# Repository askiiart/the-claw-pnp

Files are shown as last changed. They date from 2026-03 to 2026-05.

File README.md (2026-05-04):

# The Claw - pick-and-place head

A relatively cheap way to do manual pick and place by converting a 3D printer.

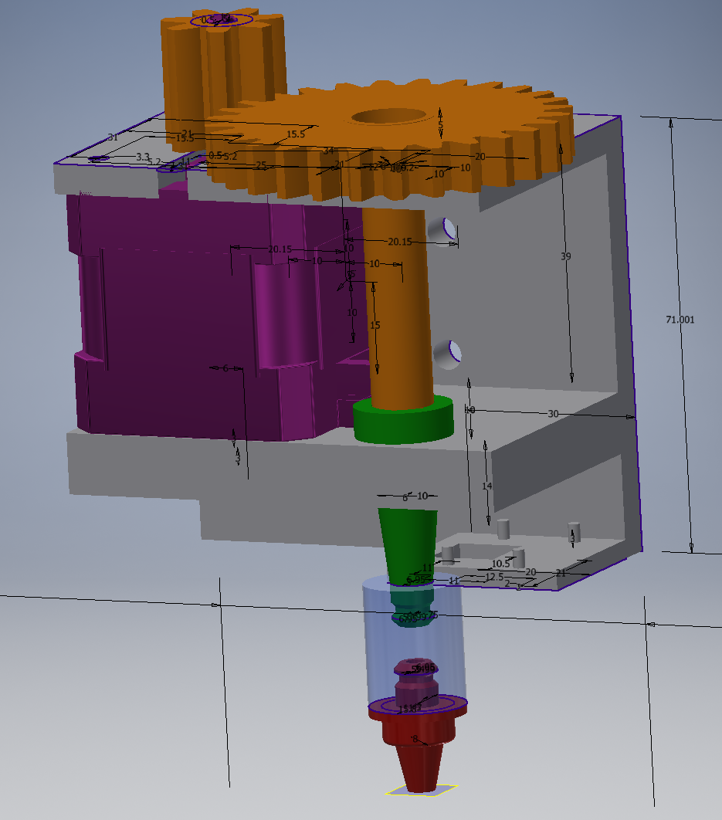
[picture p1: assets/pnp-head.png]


## Control/software

This just uses whatever Pi camera streaming software you want, plus Octoprint/serial to control it, like any printer. No special firmware is generally required (depending on your specific wiring). Octopi works great for this, as it provides both a camera view and serial/controls.

## Assembly

Just print all the parts, then assemble it all together. **Important**: Make sure you install the head on the printer before assembly, as the stepper motor blocks the screws.

Note: The solenoid controls vacuum on/off, that's not included on the head as it's extra weight as well as being hard to mount - put it near the air pump.

## Head assembly

- Screw in the stepper motor from the top
- Install the lower shaft (green) by just setting it in the bottom

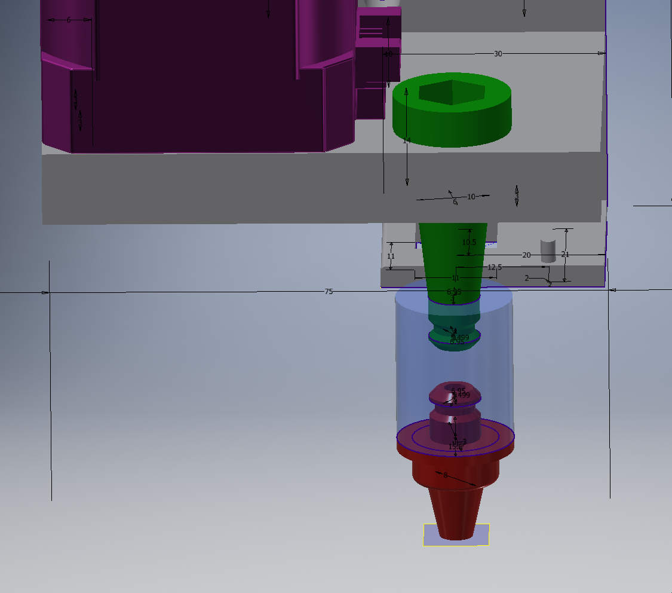
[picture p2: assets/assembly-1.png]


- There is a spring resting between the lower shaft and the roof (not shown in image). Install the upper shaft into the hole, connecting to the lower shaft, then install the small gear onto the stepper motor.

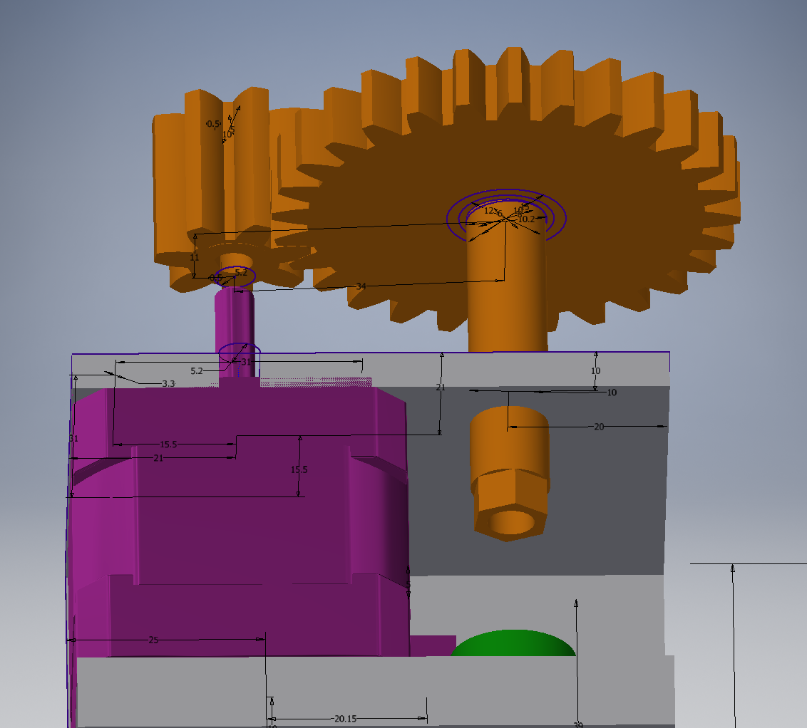
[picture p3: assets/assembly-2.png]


The nozzle is mounted using a silicone connector which has the lower shaft tip (juki nozzle connector) on one side, and the nozzle on the other to ensure proper fit. The silicone is used to make nozzles fit snugly - creating the mold is left as an exercise to the reader, as molding off a real nozzle will give the best results.

## Wiring

Your wiring can vary significantly, but the only control besides just basic movement is turning the solenoid on/off. If your fan headers can provide enough current, that will be the easiest way to control it.

## Parts

| Item name | Price | Quantity | Link | Total |
| --- | ----- | --- | --- | --- |
| NEMA 17 motor (XH) | 7.06  | 1 | <https://www.aliexpress.us/item/3256808273084374.html> | 7.06 |
| Spring (45x13) | 3.17  | 1 | <https://www.aliexpress.us/item/3256808172121056.html> | 3.17 |
| 6x8 5m tubing | 5.46  | 1 | <https://www.aliexpress.us/item/3256809523563550.html> | 5.46 |
| 24V Air pump | 11.4  | 1 | <https://www.aliexpress.us/item/3256807520990953.html> | 11.4 |
| Silicone | 25.62 | 1 | <https://www.amazon.com/BBDINO-Elastic-Silicone-Making-Casting/dp/B0DK9GD52Q> | 25.62 |
| AF-65 camera | 4.65  | 1 | <https://www.aliexpress.us/item/3256803200476731.html> | 4.65 |
| Solenoid | 5.88  | 1 | <https://www.aliexpress.us/item/3256807858795768.html> | 5.88 |
| 8x12x3.5mm bearing | 2.51  | 1 | <https://www.aliexpress.us/item/3256807442294068.html> | 2.51 |
| Blunt needles (nozzles) | 7.99  | 1 | <https://www.amazon.com/Dispensing-Industrial-Dispenser-Stainless-Adhesive/dp/B09CL4RB5X> | 7.99 |
| | | | | |
| | | | | |
| | | | | |
| Total | | | | 79.82355 |

---

Note: if trying to create an exploded view for assembly instructions, you want "Mate:9" - set it to e.g. 25mm.

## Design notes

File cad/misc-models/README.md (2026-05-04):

# Misc models

Models off grabcad and whatnot, just used for display in assembly and whatnot.

- [17HS4401](https://grabcad.com/library/17hs4401-1)

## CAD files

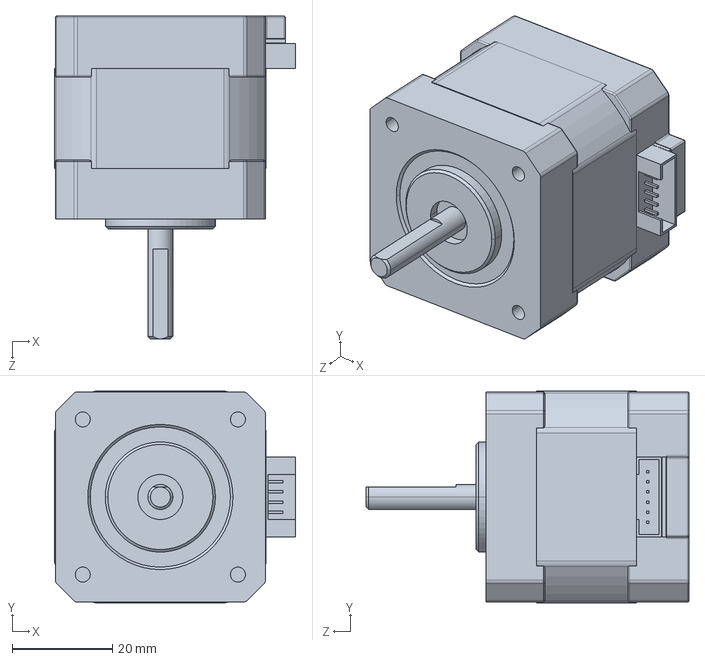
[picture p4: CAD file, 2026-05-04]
cad/misc-models/17HS4401.STEP
48.2 x 42.3 x 64.5 mm

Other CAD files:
cad/3mm-nozzle-assembly.iam
cad/5mm-nozzle-assembly.iam
cad/8mm-nozzle-assembly.iam
cad/gear-assembly.iam
cad/gear-assembly/Design Accelerator/Spur Gear11.ipt
cad/gear-assembly/Design Accelerator/Spur Gear21.ipt
cad/gear-assembly/Design Accelerator/Spur Gears1.iam
cad/juki-head-assembly.iam
cad/juki-mount.ipt
cad/juki-nozzle-base.ipt
cad/literally-just-a-cylinder-for-assembly-mockup-(silicone-sleeve).ipt
cad/literally-just-a-sketch.ipt
cad/misc-models/17HS4401.ipt
cad/motor-gear-base.ipt
cad/nozzle-3mm-tip.ipt
cad/nozzle-5mm-dip.ipt
cad/nozzle-8mm-dip.ipt
cad/pnp-head-assembly.iam
cad/pnp-head-assembly/Design Accelerator/Spur Gear12.ipt
cad/pnp-head-assembly/Design Accelerator/Spur Gear14.ipt
cad/pnp-head-assembly/Design Accelerator/Spur Gear22.ipt
cad/pnp-head-assembly/Design Accelerator/Spur Gear24.ipt
cad/pnp-head-assembly/Design Accelerator/Spur Gears2.iam
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

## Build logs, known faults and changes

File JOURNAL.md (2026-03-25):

# Journal

## 2026-03-22A - part selection and gantry plate

*1 hour*

Just had to grab the parts I had already researched prior - found motor dimensions [here](https://makers-hut.com/product/nema-8-hollow-shaft-stepper-motor-1-8deg-0-6a-18mnm-20x20x30mm-4-wire-nema8/).

motor dimensions

The image doesn't say everything, but given it's a standard NEMA 8 motor, it's easy to find dimensions

NEMA 8 dimensions

As for the gantry plate, found dimensions for that, from which I made a quick sketch of the relevant holes in Inventor.

gantry plate dimensions

holes in inventor

## 2026-03-22B - nozzle selection

*0.5 hours*

I found [this](https://groups.google.com/g/openpnp/c/s_PBSA7VQWM) usenet post, seems you can use all kinds of stuff as nozzles actually, including needles (for extruding glue and stuff). Since actual nozzles are expensive, I'll use those

## 2026-03-23A - camera selection and looked into motors more

*1 hour*

Spent some time trying to find which camera to use. Seems the best option is a pi camera-like module (65mm, autofocus, OV5647), so added that to the parts list. And given it's basically the same dimensions of a pi camera 2, I can design around that.

I also looked into motor selection more, turns out that motor I had previously selected is way too low voltage, I wouldn't be able to add a spring, and it's also more difficult to attach stuff to it given it's a smooth shaft. Instead, I'm going for a design similar to xpdiy's with a standard NEMA 17 motor, albeit with silicone to hold the nozzle for better fit, easier printing, and ease of design.

## 2026-03-23B - Designed the head, just need to design nozzle bits

*3 hours*

I designed the head, still need to design the nozzle bits but got a good start.

## 2026-03-24/25 - CAD yay

*7 hours*

So uh I actually got decent at CAD, even figured out how to do assembly somewhat competently. Not much to say here besides me just trying to figure out workarounds for Inventor being weird - I ended up creating a structure that would've made more sense as a loft by extruding and using the hole tool, and I even had to make a part that's literally just a sketch in order to align stuff in assembly.

Really not much to journal here unfortunately, besides just that I learned how to CAD half decently. Oh also fun fact apparently there isn't a single tutorial on how to use springs in Inventor, *everybody* just makes springs out of coils.

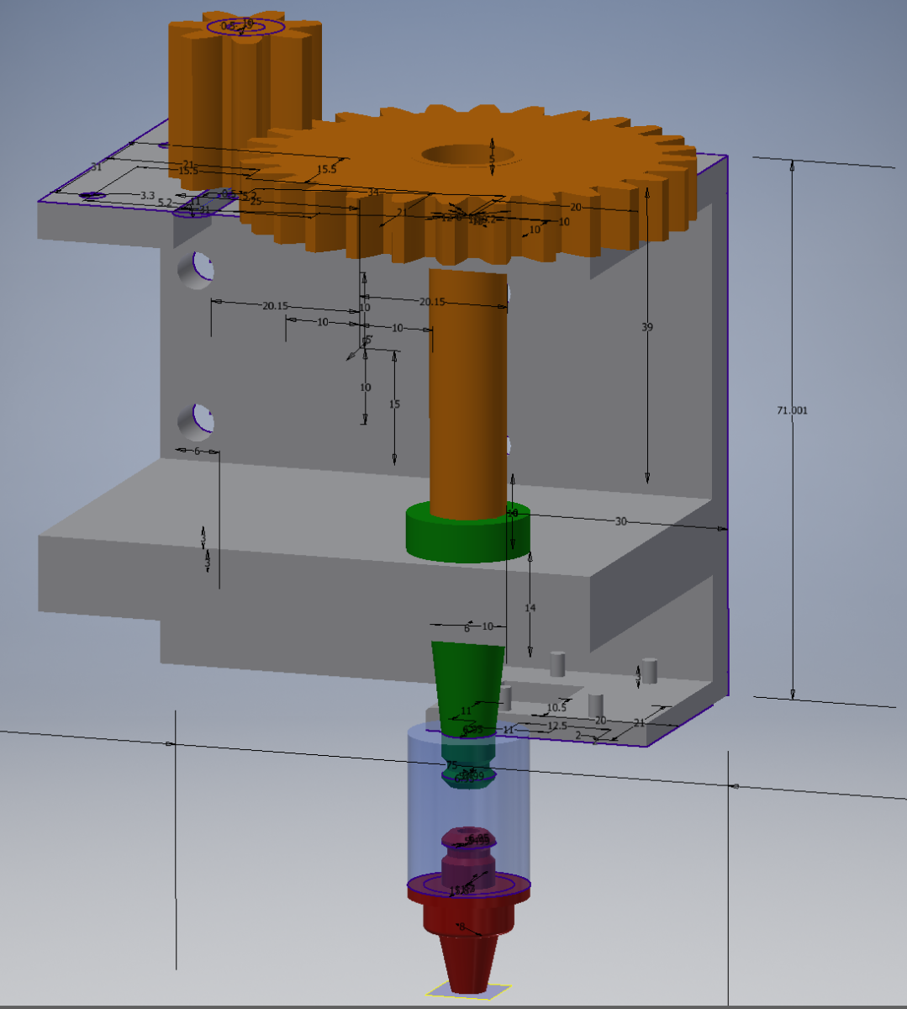
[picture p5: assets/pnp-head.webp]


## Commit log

2026-03-25 add CAD
    [3mm-nozzle-assembly.iam, 5mm-nozzle-assembly.iam, 8mm-nozzle-assembly.iam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]
2026-03-25 add BOM
    [BOM.csv, BOM.xlsx]
2026-03-25 add more explanation of control, assembly, and wiring
2026-05-04 add motor to assembly
    [17HS4401.STEP, 17HS4401.ipt, pnp-head-assembly.iam]
2026-05-04 update with better assembly instructions
